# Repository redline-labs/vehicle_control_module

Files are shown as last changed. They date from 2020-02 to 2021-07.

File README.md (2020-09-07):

# Vehicle Control Module

A communication gateway and power distribution for motorsports, serving as the main electronic hub of the vehicle.

## Goals
  - Completely open-source HW and SW.  Should be a platform that anybody can hack, extend, and make their own.
  - Common parts, readily available for Digikey, Mouser, etc.  Datasheets are available without NDA.
  - Shoot for OEM level reliability and robustness, without going full ASIL alphabet soup.

## Vision
  - Controlling a circuit should be as simple as writing some logic `(engine_temp_c > 70.0f) && (vehicle_speed_mps < 5.0f)`.
  - No need for traditional fuses, relays as something like a slow-blow fuse can be done in software.
  - Plug into the vehicle using standard ethernet to debug/reconfigure/reflash.
  - Foundation for support datalogging, telemetry, and HMI.

## Hardware
Based on the Microchip [ATSAMV71Q21](https://www.microchip.com/wwwproducts/en/ATSAMV71Q21).
* (2) CAN-FD channels via [TLE9250](https://www.infineon.com/cms/en/product/transceivers/automotive-transceiver/automotive-can-transceivers/tle9250xsj/).
* (3) 100BASE-T1 channels via [TJA1100](https://www.nxp.com/products/interfaces/ethernet-/automotive-ethernet-phy-transceivers/ieee-100base-t1-compliant-automotive-ethernet-phy-transceiver:TJA1100HN).
* (1) 100BASE-TX channel via [KSZ8061MNX](https://www.microchip.com/wwwproducts/en/KSZ8061) to support debug with a laptop.
* (18) High Side drivers via [BTS50015-1TAD](https://www.infineon.com/cms/en/product/power/smart-low-side-high-side-switches/automotive-smart-high-side-switch-profet/power-profet/bts50015-1tad/).
* (2) RS-232 serial channels to connect GPS receivers and legacy IMUs.
* (8) Digital Inputs.

## Prerequisites
### MacOS
```
wget https://armkeil.blob.core.windows.net/developer/Files/downloads/gnu-rm/10-2020q2/gcc-arm-none-eabi-10-2020-q2-preview-mac.pkg

# Install.  Add `/Applications/ARM/bin/` to PATH via bash_profile.

brew install cmake
```

## Building
```
# Jump into the sw directory, create a build dir, and then jump into that.
cd sw
mkdir build
cd build

# Run CMake specifying the toolchain file.
cmake ..

# Build!
make
```

## Debugging
A configuration script under `conf/j-link` can be used with Segger Ozone to load the generated ELF on target and debug.

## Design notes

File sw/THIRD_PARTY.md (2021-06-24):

||Name||Version||License||Link||
|lua|5.4.0|MIT|https://www.lua.org/home.html|
|Advanced Software Framework|3.48|Atmel ASF License|https://www.microchip.com/mplab/avr-support/avr-and-sam-downloads-archive|
|FreeRTOS|10.4.3|MIT|https://www.freertos.org/index.html|
|FreeRTOS-Plus-TCP|2.3.3|MIT|https://www.freertos.org/index.html|

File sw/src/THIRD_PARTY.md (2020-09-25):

||Name||Version||License||Link||
|lua|5.4.0|MIT|https://www.lua.org/home.html|
|Advanced Software Framework|Atmel ASF License|https://www.microchip.com/mplab/avr-support/advanced-software-framework|
|FreeRTOS|10.4.1|MIT|https://www.freertos.org/index.html|

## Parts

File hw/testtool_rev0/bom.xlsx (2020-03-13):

Parts | Qty | Value | Package | Device | Description | MANUFACTURER_NAME | MANUFACTURER_PART_NUMBER | MOUSER_PART_NUMBER
C1, C3, C9, C92, C95 | 5 | 10uF | C0603 | GRM188R6YA106MA73J | CAPACITOR, American symbol
C101 | 1 | 0.47uF | C0603 | C1608X7R1H474K080AC | CAPACITOR, American symbol
C102 | 1 | 220nF | C0805 | C0805X223K1RECAUTO | CAPACITOR, American symbol
C16, C90, C93 | 3 | 4.7nF | C0603 | C1608C0G2A472J080AE | CAPACITOR, American symbol
C18, C87, C103, C105, C107 | 5 | 10uF | C0805 | GRM21BC8YA106ME11L | CAPACITOR, American symbol
C19, C20 | 2 | 8.2pF | C0603 | GCM1885C2A8R2DA16D | CAPACITOR, American symbol
C2, C7, C10, C11, C14, C15, C17, C66, C68, C69, C70, C75, C76, C77, C78, C91, C94, C146, C147, C156, C157, C158, C159, C160, C161, C163, C164, C166, C167, C168, C169, C170, C171, C172 | 34 | 100nF | C0603 | GCM1887U1H103JA16J | CAPACITOR, American symbol
C21, C22 | 2 | 12pF | C0603 | C0603C120K5GACTU | CAPACITOR, American symbol
C4, C5, C8, C12, C106, C162 | 6 | 1uF | C0603 | GMJ107CB7105MAHR | CAPACITOR, American symbol
C6, C13 | 2 | 47pF | C0603 | C0603C470J1GACAUTO | CAPACITOR, American symbol
C67 | 1 | 3.3uF | C0603 | C1608X5R1V335M080AC | CAPACITOR, American symbol
C71, C72, C165 | 3 | 4.7uF | C0603 | C1608JB1V475K080AC | CAPACITOR, American symbol
C73, C74 | 2 | 18nF | C0603 | GCM188R72A183KA37J | CAPACITOR, American symbol
C83, C88 | 2 | 0.47uF | C0805 | GCM21BR71H474KA55K | CAPACITOR, American symbol
C84, C85, C99, C100 | 4 | 470pF | C0805 | GCM21A5C2E471JX01D | CAPACITOR, American symbol
C86 | 1 | UCZ1K151MNQ1MS | CAPAE1360X1450N | UCZ1K151MNQ1MS | Aluminum Electrolytic Capacitors - SMD 80V 150UF 20% | Nichicon | UCZ1K151MNQ1MS | 647-UCZ1K151MNQ1MS
D1 | 1 | PESD2ETH-AXR | PESD2ETHAXR | PESD2ETH-AXR | ESD Suppressors / TVS Diodes PESD2ETH-AX/SOT4/REEL 7 Q3/T4" | Nexperia | PESD2ETH-AXR | 771-PESD2ETH-AXR
D4, D5, D6, D9 | 4 | PMEG3030EP,115 | SODFL4725X110N | PMEG3030EP,115 | Nexperia PMEG3030EP,115 SMT Schottky Diode, 30V 3A, 2-Pin SOD128 | Nexperia | PMEG3030EP,115 | 771-PMEG3030EP115
D7, D8 | 2 | SMAJ24CA-Q | DIONM5127X229N | SMAJ24CA-Q | Bourns SMAJ24CA-Q, Bi-Directional TVS Diode, 400W, 2-Pin DO-214AC | Bourns | SMAJ24CA-Q | 652-SMAJ24CA-Q
FL1 | 1 | ACT45L-201-2P-TL000 | ACT45L_1 | ACT45L-201-2P-TL000 | Common mode choke SMD 200uH 100mA 50V TDK ACT Series Shielded SMD Common Mode Line Filter 200 uH -30 %, 50 % 100mA Idc | TDK | ACT45L-201-2P-TL000 | 810-ACT45L2012PTL000
FL2, FL3, FL4 | 3 | BLM18PG330SN1D | BEADC1608X95N | BLM18PG330SN1D | BLM18_N1D Series EMI Suppression Filter 33+/-25% at 100MHz 3A @85 | Murata Electronics | BLM18PG330SN1D | 81-BLM18PG330SN1D
IC1 | 1 | SST26VF032BT-104I_SM | SOIC127P794X203-8N | SST26VF032BT-104I_SM | Microchip Technology SST26VF032BT-104I/SM 32Mbit Flash Memory Chip, 8-Pin SOIJ | Microchip | SST26VF032BT-104I/SM | 579-T26VF032BT104ISM
IC13, IC18 | 2 | TLE9250XSJXUMA1 | SOIC127P602X173-8N | TLE9250XSJXUMA1 | CAN Interface IC TRANSCEIVER | Infineon | TLE9250XSJXUMA1 | 726-TLE9250XSJXUMA1
IC2 | 1 | ATSAMV71Q21B-AABT | QFP50P2200X2200X160-144N | ATSAMV71Q21B-AABT | ARM Microcontrollers - MCU 2MB FLASH 384KB SRAM LQFP144 T/R | Microchip | ATSAMV71Q21B-AABT | 579-ATSAMV71Q21BAABT
IC3 | 1 | TJA1100HNZ | QFN50P600X600X100-37N | TJA1100HNZ | NXP - TJA1100HNZ - ETHERNET PHY, AEC-Q100, 100MBPS, HVQFN36 | Nexperia | TJA1100HNZ | 771-TJA1100HNZ
IC4 | 1 | FT2232HL | QFP50P1200X1200X160-64N | FT2232HL | Dual High Speed USB UART/FIFO IC, LQFP64 FTDI Chip FT2232HL Dual UART Interface RS232, RS422, RS485 480Mbit/s, 64-Pin, LQFP | FTDI Chip | FT2232HL
J1, J2 | 2 | 2305018-2 | TE_2305018-2 | 2305018-2 | TYPE C Right Angle Sealable SMT IPX8 3.1 GEN 2 Wire to Board USB | TE Connectivity
J3, J4, J5, J6 | 4 | TBL009-254-04GY-2GY | TBL00925404GY2GY | TBL009-254-04GY-2GY | Fixed Terminal Blocks Terminal block, screwless, 2.54, Horizontal, 4, Gray w Gray Button | CUI Devices | TBL009-254-04GY-2GY | 490-TBL00925404GY2GY
L1, L2 | 2 | 0603CS-R12XGLU | 0603CS82NXGLW | 0603CS-R12XGLU | COILCRAFT - 0603CS-R12XGLU - High Frequency Inductor, 120 nH, 0603CS Series, 300 mA, 0603 [1608 Metric], Wirewound, 0.65 ohm | COILCRAFT | 0603CS-R12XGLU | 994-0603CS-R12XGLU
L7 | 1 | XAL4020-102MEC | XAL40XX | XAL4020-102MEC | Fixed Inductors 1uH 20% 9.6A 14.60mOhms AEC-Q200 | COILCRAFT | XAL4020-102MEC | 994-XAL4020-102MEC
L8 | 1 | XAL4040-103MEC | XAL40XX | XAL4040-103MEC | Fixed Inductors XAL4040 High Current 10 uH 20 % 3.1 A | COILCRAFT | XAL4040-103MEC | 994-XAL4040-103MEC
L9 | 1 | DO3316P-103MLB | DO3316P103MLB | DO3316P-103MLB | Fixed Inductors DO3316P SMT Pwr Ind 10 uH 20 % 3.9 A | COILCRAFT | DO3316P-103MLB | 994-DO3316P-103MLB
LED1, LED4, LED5, LED6, LED7, LED11, LED12, LED13, LED14, LED15, LED16 | 11 |  | 0603 | 150060BS55040 | LED
R1, R2, R95, R96 | 4 | 60 | R0805 | ERJ-U06F60R4V | RESISTOR, American symbol
R24 | 1 | 100k | R0603 | SFR03EZPF1003 | RESISTOR, American symbol
R26, R82 | 2 | 0 | R0603 | RCS06030000Z0EC | RESISTOR, American symbol
R3, R19, R20, R21 | 4 | 49.9 | R0603 | ERJ-3EKF49R9V | RESISTOR, American symbol
R4, R22, R23 | 3 | 1k | R0603 |  | RESISTOR, American symbol
R5, R7, R10, R12, R13, R16, R18, R25, R83, R98, R103, R104, R183, R188, R193, R195, R196, R197 | 18 | 10k | R0603 |  | RESISTOR, American symbol
R6, R8, R11, R14, R15, R17 | 6 | DNP | R0603 |  | RESISTOR, American symbol
R85, R88, R89, R90, R91, R92 | 6 | 12k | R0603 | ERJ-PB3B1202V | RESISTOR, American symbol
R9, R31, R32, R86, R87 | 5 | 5.11k | R0603 | ERJ-S03F5111V | RESISTOR, American symbol
R97 | 1 | 1k | R0805 | ERJ-PB6B1001V | RESISTOR, American symbol
TC1 | 1 | TC2050-IDC | TC2050-IDC | TC2050-IDC | Tag-Connect In Circuit Programming & Debug Cable 10 Pin
U2 | 1 | LM63625 | PWP0016K_L | LM63625DQPWPRQ1 |  | Texas Instruments | LM63625DQPWPTQ1
U3 | 1 | TPS62007-Q1_DGS_10 | DGS10 | TPS62007-Q1_DGS_10 | Automotive Catalog High-Efficiency Step-Down Low Power DC-DC Converter | Texas Instruments | TPS62007-Q1_DGS_10
Y1 | 1 | NX3225SA-25MHZ-EXS00A-CS11338 | NX3225SA25MHZEXS00ACS11338 | NX3225SA-25MHZ-EXS00A-CS11338 | CRYSTAL 25MHZ 18PF SMD | NDK | NX3225SA-25MHZ-EXS00A-CS11338
Y2 | 1 | ABM8AIG-12.000MHZ-12-D2Z-T | ABM8AIG12000MHZ12D2ZT | ABM8AIG-12.000MHZ-12-D2Z-T | ABRACON - ABM8AIG-12.000MHZ-12-D2Z-T - CRYSTAL, AECQ200, 12MHZ, 12PF, 3.2X2.5MM | ABRACON | ABM8AIG-12.000MHz-12-D2Z-T | 815-ABM8AIG1212D2ZT
Y3 | 1 | ABM8AIG-12.000MHZ-1Z-T | ABM8AIG25000MHZ122ZT3 | ABM8AIG-12.000MHZ-1Z-T | Crystals 18pF 12MHz 10ppm AEC-Q200 -40C +125C | ABRACON | ABM8AIG-12.000MHZ-1Z-T | 815-M8AIG-12-1ZT

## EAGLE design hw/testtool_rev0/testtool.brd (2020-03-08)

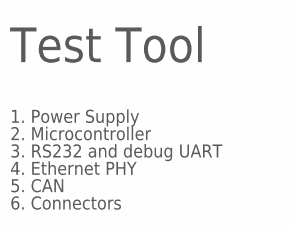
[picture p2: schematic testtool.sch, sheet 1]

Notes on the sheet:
Test Tool
1. Power Supply
2. Microcontroller
3. RS232 and debug UART
4. Ethernet PHY
5. CAN
6. Connectors

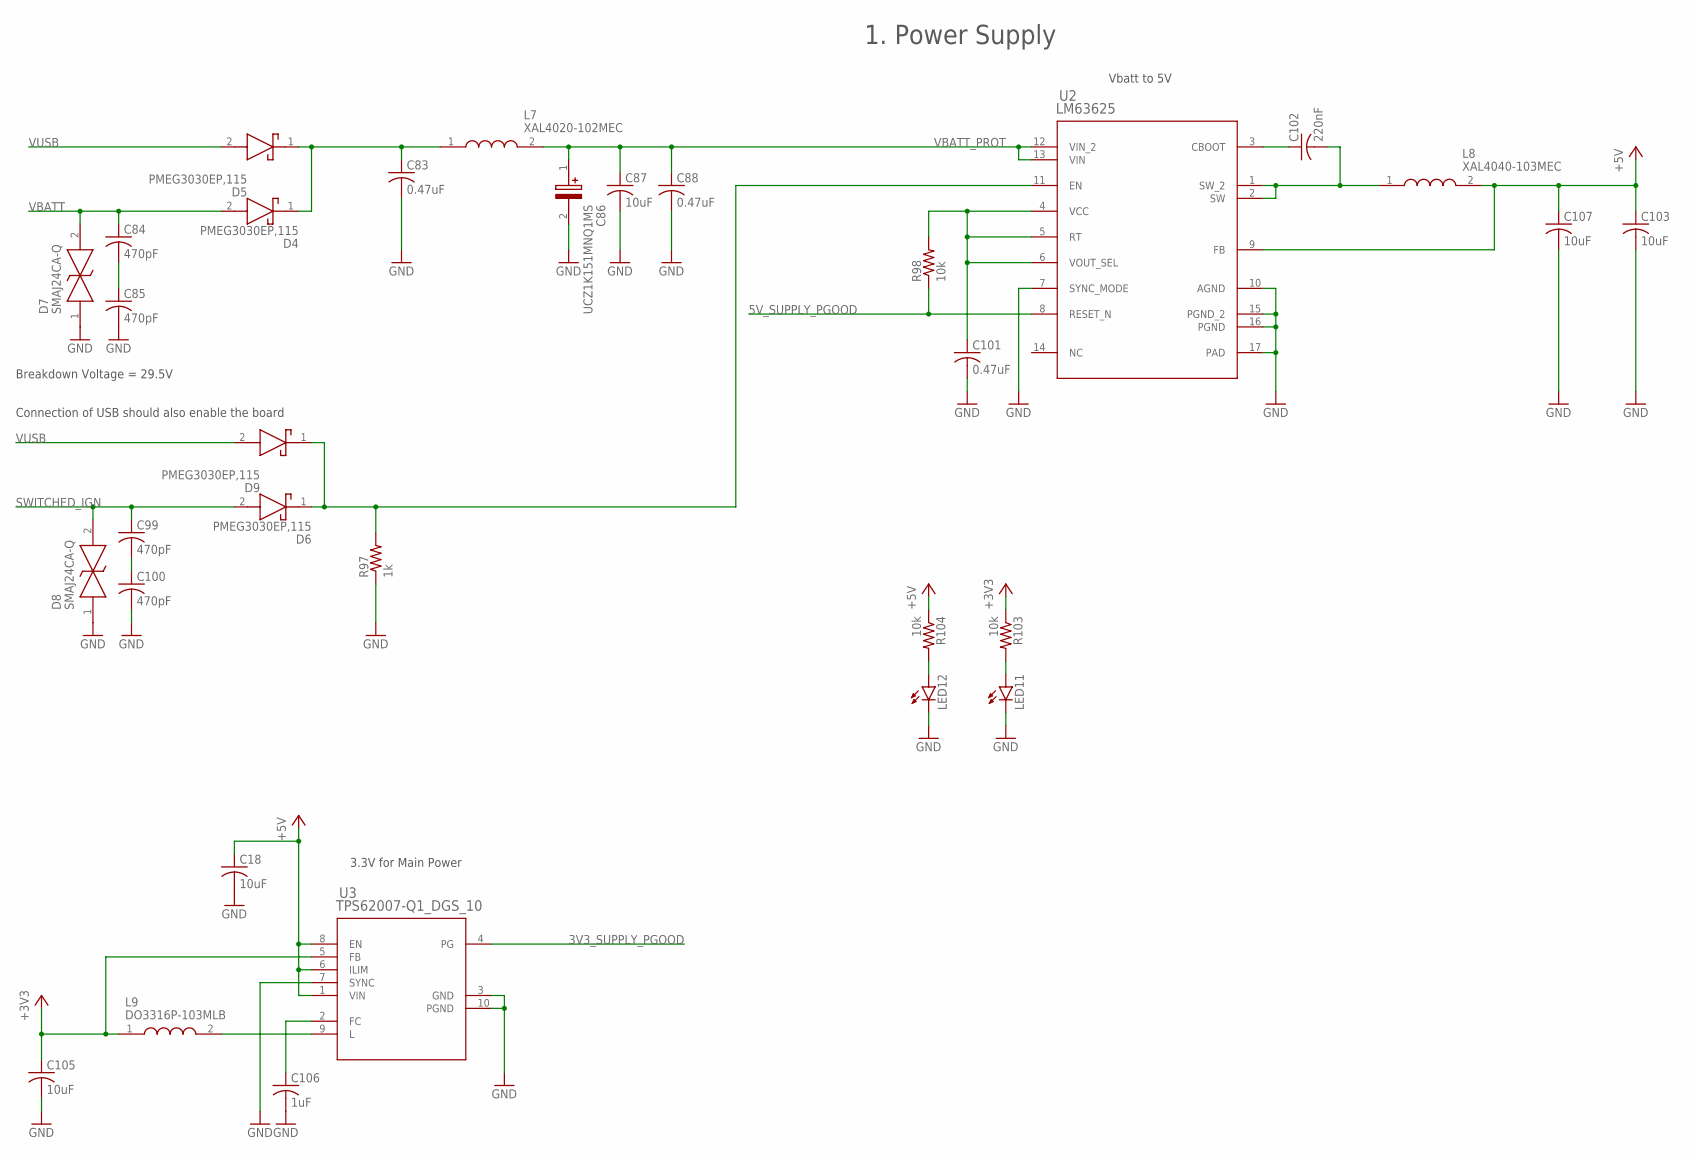
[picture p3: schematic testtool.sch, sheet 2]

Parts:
C18, C87, C103, C105, C107: 10uF; C0805
C83, C88: 0.47uF; C0805
C84, C85, C99, C100: 470pF; C0805
C86: UCZ1K151MNQ1MS; CAPAE1360X1450N
C101: 0.47uF; C0603
C102: 220nF; C0805
C106: 1uF; C0603
D4, D5, D6, D9: PMEG3030EP,115; SODFL4725X110N
D7, D8: SMAJ24CA-Q; DIONM5127X229N
L7: XAL4020-102MEC; XAL40XX
L8: XAL4040-103MEC; XAL40XX
L9: DO3316P-103MLB; DO3316P103MLB
LED11, LED12: LEDCHIPLED_0603; CHIPLED_0603
R97: 1k; R0805
R98, R103, R104: 10k; R0603
U2: LM63625; PWP0016K_L
U3: TPS62007-Q1_DGS_10; DGS10

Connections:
3V3_SUPPLY_PGOOD: U3.4 (PG); also elsewhere on the board
5V_SUPPLY_PGOOD: R98.1, U2.8 (RESET_N)
+3V3: C105.1, L9.1, R103.1, U3.5 (FB); also elsewhere on the board
+5V: C18.1, C103.1, C107.1, L8.2, R104.1, U2.9 (FB), U3.1 (VIN), U3.6 (ILIM), U3.8 (EN); also elsewhere on the board
GND: C18.2, C83.2, C85.2, C86.2 (-), C87.2, C88.2, C100.2, C101.2, C103.2, C105.2, C106.2, C107.2, D7.1, D8.1, LED11.C, LED12.C, R97.1, U2.7 (SYNC_MODE), U2.10 (AGND), U2.15 (PGND_2), U2.16 (PGND), U2.17 (PAD), U3.3 (GND), U3.7 (SYNC), U3.10 (PGND); also elsewhere on the board
unnamed: C99.2, C100.1
unnamed: D6.1 (K), D9.1 (K), R97.2, U2.11 (EN)
unnamed: C83.1, D4.1 (K), D5.1 (K), L7.1
unnamed: C84.2, C85.1
unnamed: C101.1, R98.2, U2.4 (VCC), U2.5 (RT), U2.6 (VOUT_SEL)
unnamed: L9.2, U3.9 (L)
unnamed: C102.2, L8.1, U2.1 (SW_2), U2.2 (SW)
unnamed: C106.1, U3.2 (FC)
unnamed: C102.1, U2.3 (CBOOT)
unnamed: LED11.A, R103.2
unnamed: LED12.A, R104.2
SWITCHED_IGN: C99.1, D6.2 (A), D8.2; also elsewhere on the board
VBATT: C84.1, D4.2 (A), D7.2; also elsewhere on the board
VBATT_PROT: C86.1 (+), C87.1, C88.1, L7.2, U2.12 (VIN_2), U2.13 (VIN)
VUSB: D5.2 (A), D9.2 (A); also elsewhere on the board

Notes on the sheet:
1. Power Supply
Vbatt to 5V
3.3V for Main Power
Breakdown Voltage = 29.5V
Connection of USB should also enable the board

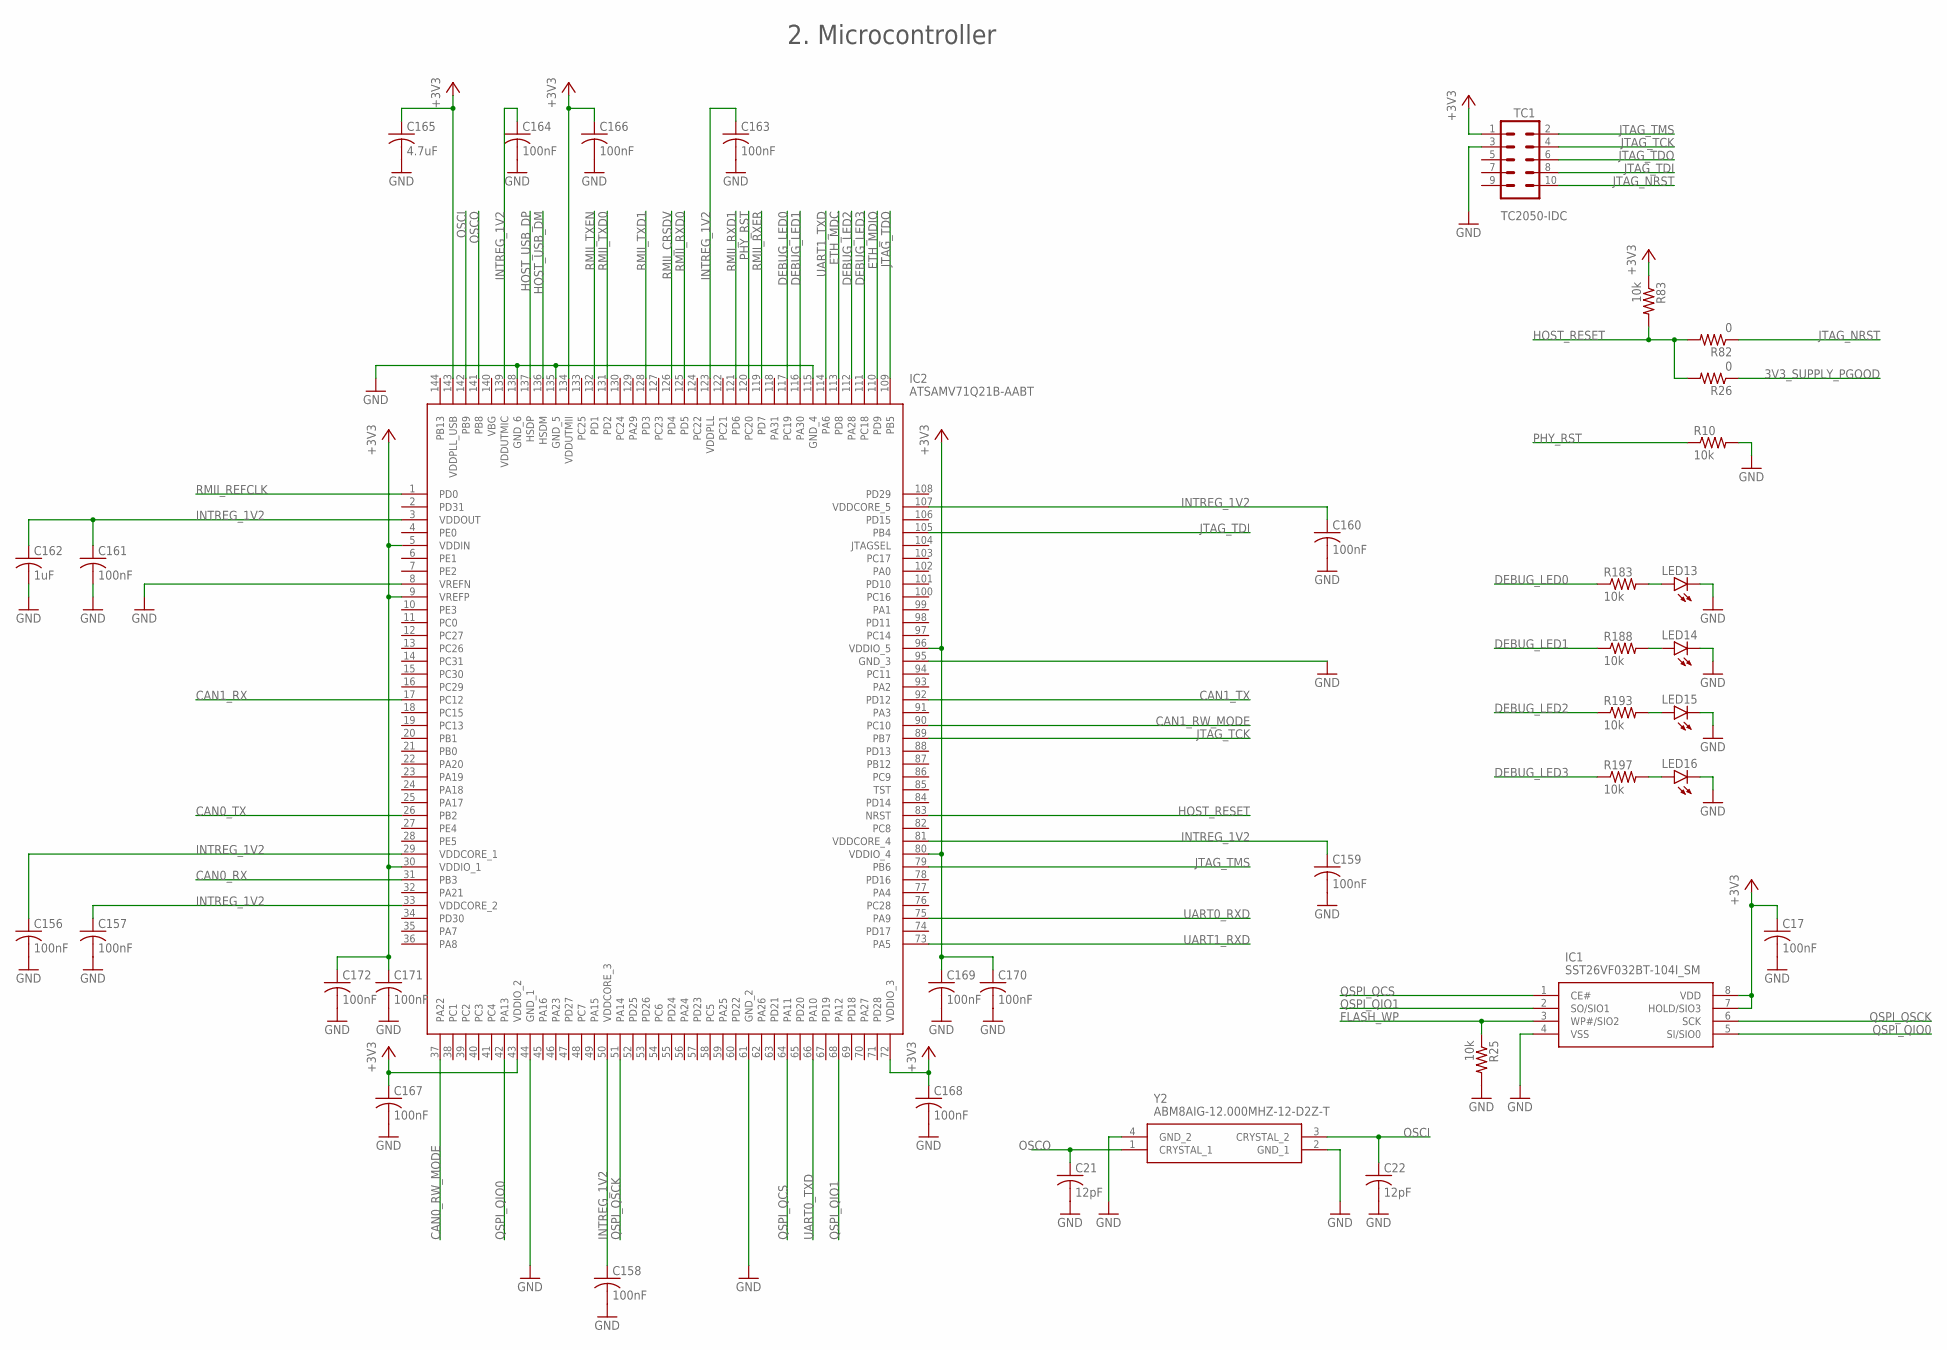
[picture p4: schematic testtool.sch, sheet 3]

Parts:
C17, C156, C157, C158, C159, C160, C161, C163, C164, C166, C167, C168, C169, C170, C171, C172: 100nF; C0603
C21, C22: 12pF; C0603
C162: 1uF; C0603
C165: 4.7uF; C0603
IC1: SST26VF032BT-104I_SM; SOIC127P794X203-8N
IC2: ATSAMV71Q21B-AABT; QFP50P2200X2200X160-144N
LED13, LED14, LED15, LED16: LEDCHIPLED_0603; CHIPLED_0603
R10, R25, R83, R183, R188, R193, R197: 10k; R0603
R26, R82: 0; R0603
TC1: TC2050-IDC
Y2: ABM8AIG-12.000MHZ-12-D2Z-T; ABM8AIG12000MHZ12D2ZT

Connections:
3V3_SUPPLY_PGOOD: R26.1; also elsewhere on the board
+3V3: C17.1, C165.1, C166.1, C167.1, C168.1, C169.1, C170.1, C171.1, C172.1, IC1.7 (HOLD/SIO3), IC1.8 (VDD), IC2.5 (VDDIN), IC2.9 (VREFP), IC2.30 (VDDIO_1), IC2.43 (VDDIO_2), IC2.72 (VDDIO_3), IC2.80 (VDDIO_4), IC2.96 (VDDIO_5), IC2.134 (VDDUTMII), IC2.143 (VDDPLL_USB), R83.1, TC1.1; also elsewhere on the board
CAN0_RW_MODE: IC2.37 (PA22); also elsewhere on the board
CAN0_RX: IC2.31 (PB3); also elsewhere on the board
CAN0_TX: IC2.26 (PB2); also elsewhere on the board
CAN1_RW_MODE: IC2.90 (PC10); also elsewhere on the board
CAN1_RX: IC2.17 (PC12); also elsewhere on the board
CAN1_TX: IC2.92 (PD12); also elsewhere on the board
DEBUG_LED0: IC2.117 (PC19), R183.1
DEBUG_LED1: IC2.116 (PA30), R188.1
DEBUG_LED2: IC2.112 (PA28), R193.1
DEBUG_LED3: IC2.111 (PC18), R197.1
ETH_MDC: IC2.113 (PD8); also elsewhere on the board
ETH_MDIO: IC2.110 (PD9); also elsewhere on the board
FLASH_WP: IC1.3 (WP#/SIO2), R25.1
GND: C17.2, C21.2, C22.2, C156.2, C157.2, C158.2, C159.2, C160.2, C161.2, C162.2, C163.2, C164.2, C165.2, C166.2, C167.2, C168.2, C169.2, C170.2, C171.2, C172.2, IC1.4 (VSS), IC2.8 (VREFN), IC2.44 (GND_1), IC2.61 (GND_2), IC2.95 (GND_3), IC2.115 (GND_4), IC2.135 (GND_5), IC2.138 (GND_6), LED13.C, LED14.C, LED15.C, LED16.C, R10.2, R25.2, TC1.3, Y2.2 (GND_1), Y2.4 (GND_2); also elsewhere on the board
HOST_RESET: IC2.83 (NRST), R26.2, R82.2, R83.2
HOST_USB_DM: IC2.136 (HSDM); also elsewhere on the board
HOST_USB_DP: IC2.137 (HSDP); also elsewhere on the board
INTREG_1V2: C156.1, C157.1, C158.1, C159.1, C160.1, C161.1, C162.1, C163.1, C164.1, IC2.3 (VDDOUT), IC2.29 (VDDCORE_1), IC2.33 (VDDCORE_2), IC2.50 (VDDCORE_3), IC2.81 (VDDCORE_4), IC2.107 (VDDCORE_5), IC2.123 (VDDPLL), IC2.139 (VDDUTMIC)
JTAG_NRST: R82.1, TC1.10
JTAG_TCK: IC2.89 (PB7), TC1.4
JTAG_TDI: IC2.105 (PB4), TC1.8
JTAG_TDO: IC2.109 (PB5), TC1.6
JTAG_TMS: IC2.79 (PB6), TC1.2
unnamed: LED13.A, R183.2
unnamed: LED14.A, R188.2
unnamed: LED15.A, R193.2
unnamed: LED16.A, R197.2
OSCI: C22.1, IC2.142 (PB9), Y2.3 (CRYSTAL_2)
OSCO: C21.1, IC2.141 (PB8), Y2.1 (CRYSTAL_1)
PHY_RST: IC2.120 (PC20), R10.1; also elsewhere on the board
QSPI_QCS: IC1.1 (CE#), IC2.64 (PA11)
QSPI_QIO0: IC1.5 (SI/SIO0), IC2.42 (PA13)
QSPI_QIO1: IC1.2 (SO/SIO1), IC2.68 (PA12)
QSPI_QSCK: IC1.6 (SCK), IC2.51 (PA14)
RMII_CRSDV: IC2.126 (PD4); also elsewhere on the board
RMII_REFCLK: IC2.1 (PD0); also elsewhere on the board
RMII_RXD0: IC2.125 (PD5); also elsewhere on the board
RMII_RXD1: IC2.121 (PD6); also elsewhere on the board
RMII_RXER: IC2.119 (PD7); also elsewhere on the board
RMII_TXD0: IC2.131 (PD2); also elsewhere on the board
RMII_TXD1: IC2.128 (PD3); also elsewhere on the board
RMII_TXEN: IC2.132 (PD1); also elsewhere on the board
UART0_RXD: IC2.75 (PA9); also elsewhere on the board
UART0_TXD: IC2.66 (PA10); also elsewhere on the board
UART1_RXD: IC2.73 (PA5); also elsewhere on the board
UART1_TXD: IC2.114 (PA6); also elsewhere on the board

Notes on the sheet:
2. Microcontroller

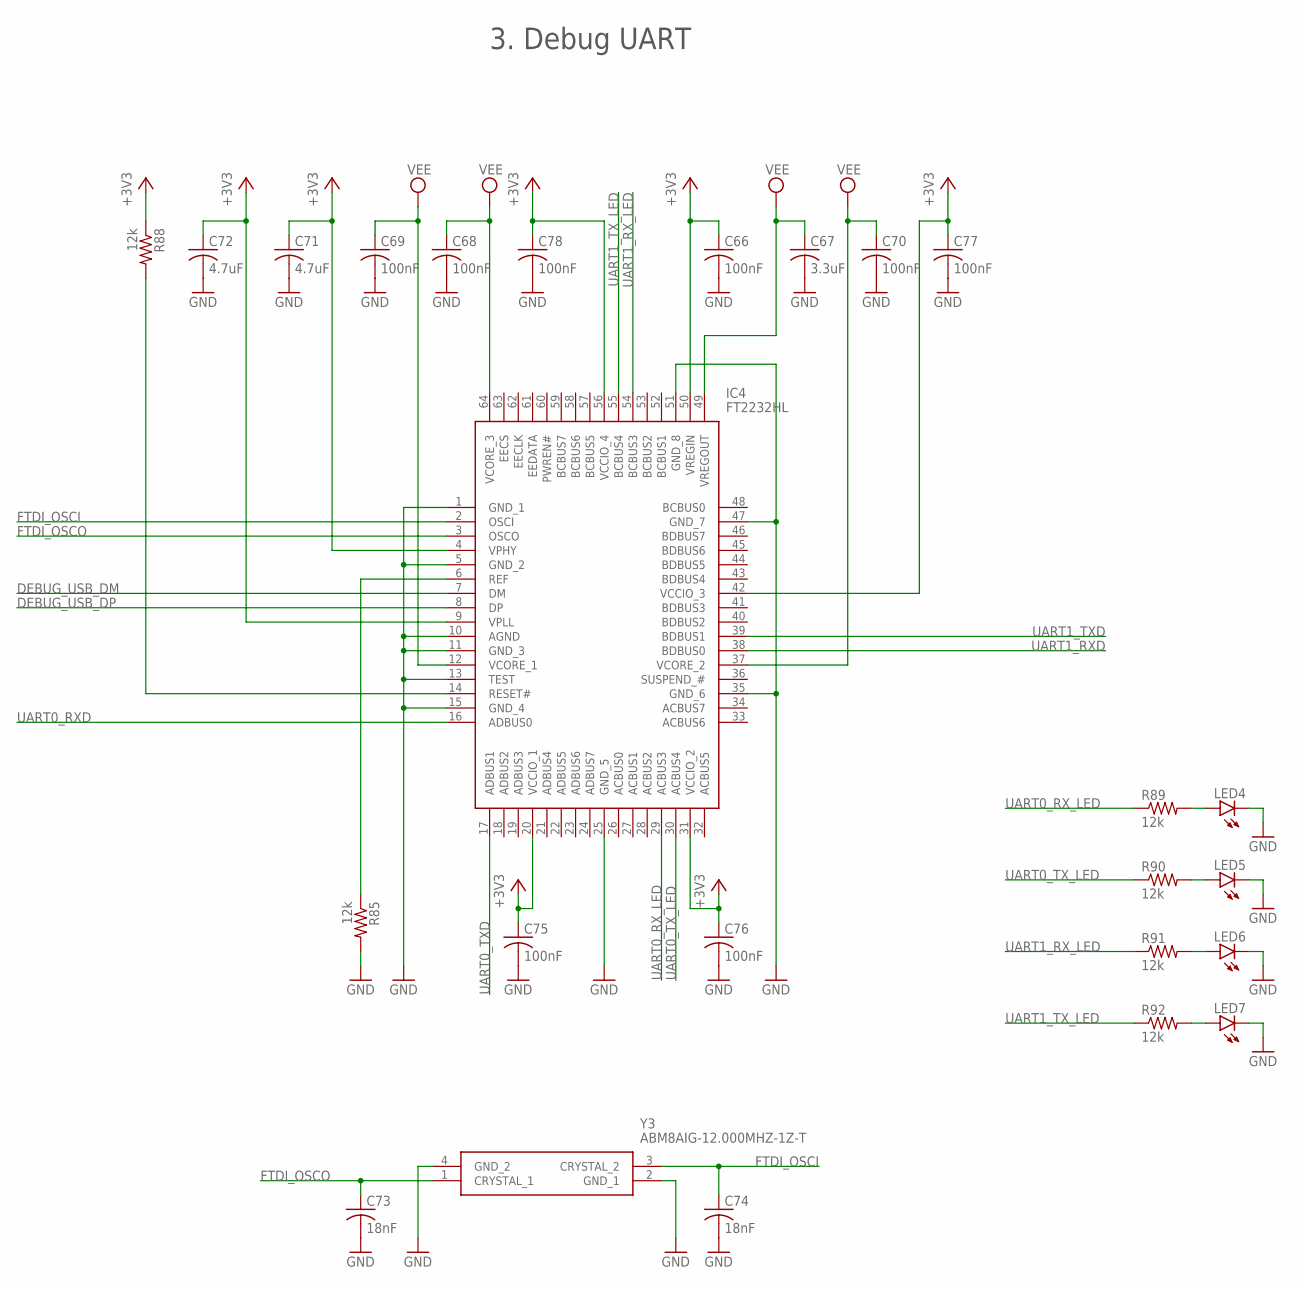
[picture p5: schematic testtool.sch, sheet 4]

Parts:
C66, C68, C69, C70, C75, C76, C77, C78: 100nF; C0603
C67: 3.3uF; C0603
C71, C72: 4.7uF; C0603
C73, C74: 18nF; C0603
IC4: FT2232HL; QFP50P1200X1200X160-64N
LED4, LED5, LED6, LED7: LEDCHIPLED_0603; CHIPLED_0603
R85, R88, R89, R90, R91, R92: 12k; R0603
Y3: ABM8AIG-12.000MHZ-1Z-T; ABM8AIG25000MHZ122ZT3

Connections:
+3V3: C66.1, C71.1, C72.1, C75.1, C76.1, C77.1, C78.1, IC4.4 (VPHY), IC4.9 (VPLL), IC4.20 (VCCIO_1), IC4.31 (VCCIO_2), IC4.42 (VCCIO_3), IC4.50 (VREGIN), IC4.56 (VCCIO_4), R88.1; also elsewhere on the board
DEBUG_USB_DM: IC4.7 (DM); also elsewhere on the board
DEBUG_USB_DP: IC4.8 (DP); also elsewhere on the board
FTDI_OSCI: C74.1, IC4.2 (OSCI), Y3.3 (CRYSTAL_2)
FTDI_OSCO: C73.1, IC4.3 (OSCO), Y3.1 (CRYSTAL_1)
GND: C66.2, C67.2, C68.2, C69.2, C70.2, C71.2, C72.2, C73.2, C74.2, C75.2, C76.2, C77.2, C78.2, IC4.1 (GND_1), IC4.5 (GND_2), IC4.10 (AGND), IC4.11 (GND_3), IC4.13 (TEST), IC4.15 (GND_4), IC4.25 (GND_5), IC4.35 (GND_6), IC4.47 (GND_7), IC4.51 (GND_8), LED4.C, LED5.C, LED6.C, LED7.C, R85.2, Y3.2 (GND_1), Y3.4 (GND_2); also elsewhere on the board
unnamed: IC4.6 (REF), R85.1
unnamed: IC4.14 (RESET#), R88.2
unnamed: LED5.A, R90.2
unnamed: LED4.A, R89.2
unnamed: LED6.A, R91.2
unnamed: LED7.A, R92.2
UART0_RXD: IC4.16 (ADBUS0); also elsewhere on the board
UART0_RX_LED: IC4.29 (ACBUS3), R89.1
UART0_TXD: IC4.17 (ADBUS1); also elsewhere on the board
UART0_TX_LED: IC4.30 (ACBUS4), R90.1
UART1_RXD: IC4.38 (BDBUS0); also elsewhere on the board
UART1_RX_LED: IC4.54 (BCBUS3), R91.1
UART1_TXD: IC4.39 (BDBUS1); also elsewhere on the board
UART1_TX_LED: IC4.55 (BCBUS4), R92.1
VEE: C67.1, C68.1, C69.1, C70.1, IC4.12 (VCORE_1), IC4.37 (VCORE_2), IC4.49 (VREGOUT), IC4.64 (VCORE_3)

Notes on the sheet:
3. Debug UART

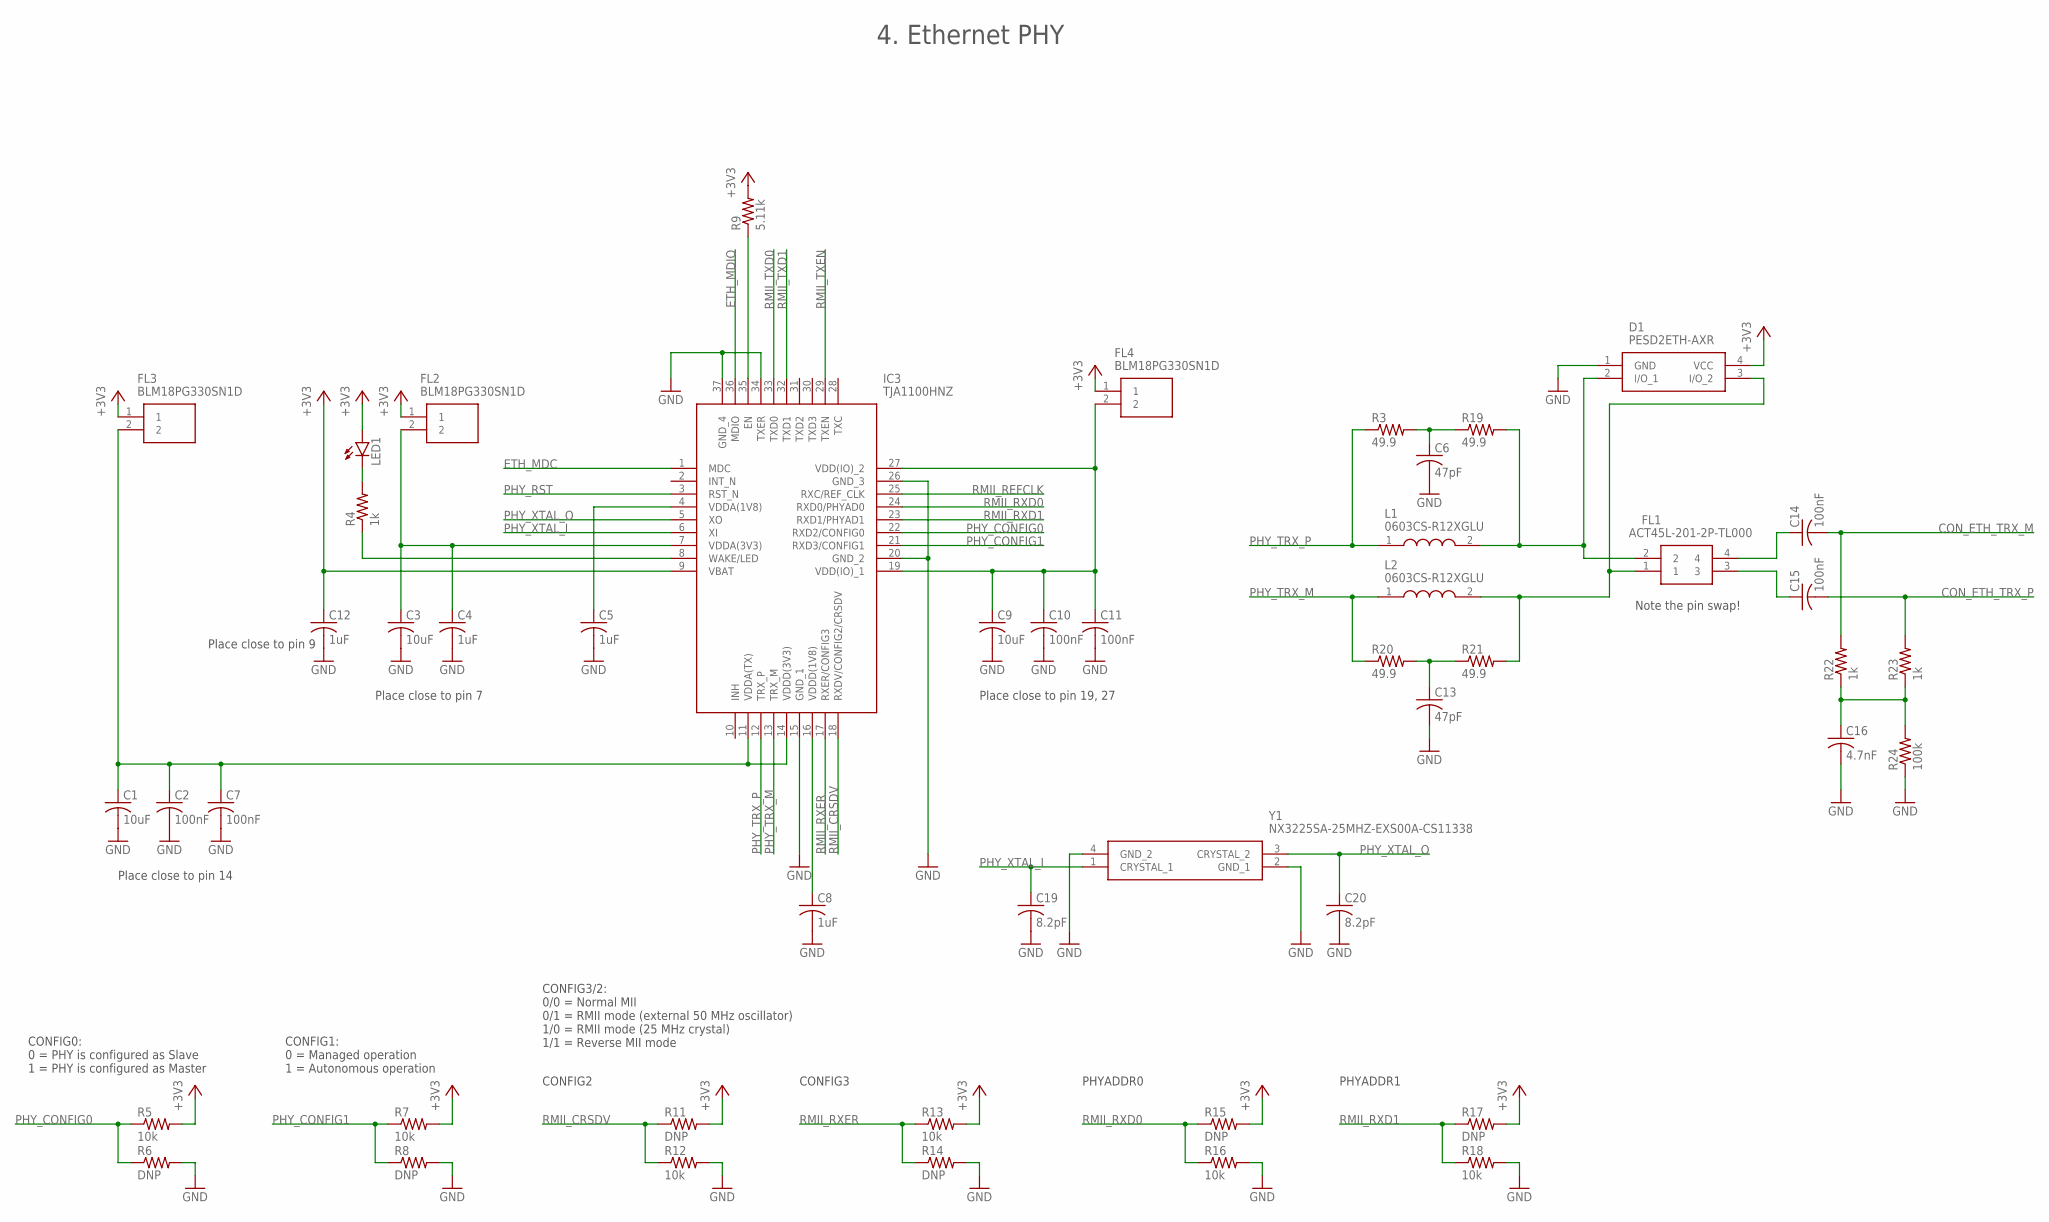
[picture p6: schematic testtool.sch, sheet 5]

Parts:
C1, C3, C9: 10uF; C0603
C2, C7, C10, C11, C14, C15: 100nF; C0603
C4, C5, C8, C12: 1uF; C0603
C6, C13: 47pF; C0603
C16: 4.7nF; C0603
C19, C20: 8.2pF; C0603
D1: PESD2ETH-AXR; PESD2ETHAXR
FL1: ACT45L-201-2P-TL000; ACT45L_1
FL2, FL3, FL4: BLM18PG330SN1D; BEADC1608X95N
IC3: TJA1100HNZ; QFN50P600X600X100-37N
L1, L2: 0603CS-R12XGLU; 0603CS82NXGLW
LED1: LEDCHIPLED_0603; CHIPLED_0603
R3, R19, R20, R21: 49.9; R0603
R4, R22, R23: 1k; R0603
R5, R7, R12, R13, R16, R18: 10k; R0603
R6, R8, R11, R14, R15, R17: DNP; R0603
R9: 5.11k; R0603
R24: 100k; R0603
Y1: NX3225SA-25MHZ-EXS00A-CS11338; NX3225SA25MHZEXS00ACS11338

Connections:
+3V3: C12.1, D1.4 (VCC), FL2.1, FL3.1, FL4.1, IC3.9 (VBAT), LED1.A, R5.2, R7.2, R9.2, R11.2, R13.2, R15.2, R17.2; also elsewhere on the board
CON_ETH_TRX_M: C14.2, R22.2; also elsewhere on the board
CON_ETH_TRX_P: C15.2, R23.2; also elsewhere on the board
ETH_MDC: IC3.1 (MDC); also elsewhere on the board
ETH_MDIO: IC3.36 (MDIO); also elsewhere on the board
GND: C1.2, C2.2, C3.2, C4.2, C5.2, C6.2, C7.2, C8.2, C9.2, C10.2, C11.2, C12.2, C13.2, C16.2, C19.2, C20.2, D1.1 (GND), IC3.15 (GND_1), IC3.20 (GND_2), IC3.26 (GND_3), IC3.34 (TXER), IC3.37 (GND_4), R6.2, R8.2, R12.2, R14.2, R16.2, R18.2, R24.1, Y1.2 (GND_1), Y1.4 (GND_2); also elsewhere on the board
unnamed: LED1.C, R4.2
unnamed: C5.1, IC3.4 (VDDA(1V8))
unnamed: IC3.8 (WAKE/LED), R4.1
unnamed: C8.1, IC3.16 (VDDD(1V8))
unnamed: C3.1, C4.1, FL2.2, IC3.7 (VDDA(3V3))
unnamed: C1.1, C2.1, C7.1, FL3.2, IC3.11 (VDDA(TX)), IC3.14 (VDDD(3V3))
unnamed: C9.1, C10.1, C11.1, FL4.2, IC3.19 (VDD(IO)_1), IC3.27 (VDD(IO)_2)
unnamed: IC3.35 (EN), R9.1
unnamed: D1.3 (I/O_2), FL1.1, L2.2, R21.2
unnamed: D1.2 (I/O_1), FL1.2, L1.2, R19.2
unnamed: C6.1, R3.2, R19.1
unnamed: C13.1, R20.2, R21.1
unnamed: C14.1, FL1.4
unnamed: C15.1, FL1.3
unnamed: C16.1, R22.1, R23.1, R24.2
PHY_CONFIG0: IC3.22 (RXD2/CONFIG0), R5.1, R6.1
PHY_CONFIG1: IC3.21 (RXD3/CONFIG1), R7.1, R8.1
PHY_RST: IC3.3 (RST_N); also elsewhere on the board
PHY_TRX_M: IC3.13 (TRX_M), L2.1, R20.1
PHY_TRX_P: IC3.12 (TRX_P), L1.1, R3.1
PHY_XTAL_I: C19.1, IC3.6 (XI), Y1.1 (CRYSTAL_1)
PHY_XTAL_O: C20.1, IC3.5 (XO), Y1.3 (CRYSTAL_2)
RMII_CRSDV: IC3.18 (RXDV/CONFIG2/CRSDV), R11.1, R12.1; also elsewhere on the board
RMII_REFCLK: IC3.25 (RXC/REF_CLK); also elsewhere on the board
RMII_RXD0: IC3.24 (RXD0/PHYAD0), R15.1, R16.1; also elsewhere on the board
RMII_RXD1: IC3.23 (RXD1/PHYAD1), R17.1, R18.1; also elsewhere on the board
RMII_RXER: IC3.17 (RXER/CONFIG3), R13.1, R14.1; also elsewhere on the board
RMII_TXD0: IC3.33 (TXD0); also elsewhere on the board
RMII_TXD1: IC3.32 (TXD1); also elsewhere on the board
RMII_TXEN: IC3.29 (TXEN); also elsewhere on the board

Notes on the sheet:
Place close to pin 7
Place close to pin 9
Place close to pin 14
Place close to pin 19, 27
CONFIG0: 0 = PHY is configured as Slave 1 = PHY is configured as Master
CONFIG1: 0 = Managed operation 1 = Autonomous operation
Note the pin swap!
4. Ethernet PHY
CONFIG3/2: 0/0 = Normal MII 0/1 = RMII mode (external 50 MHz oscillator) 1/0 = RMII mode (25 MHz crystal) 1/1 = Reverse MII mode
CONFIG2
CONFIG3
PHYADDR0
PHYADDR1

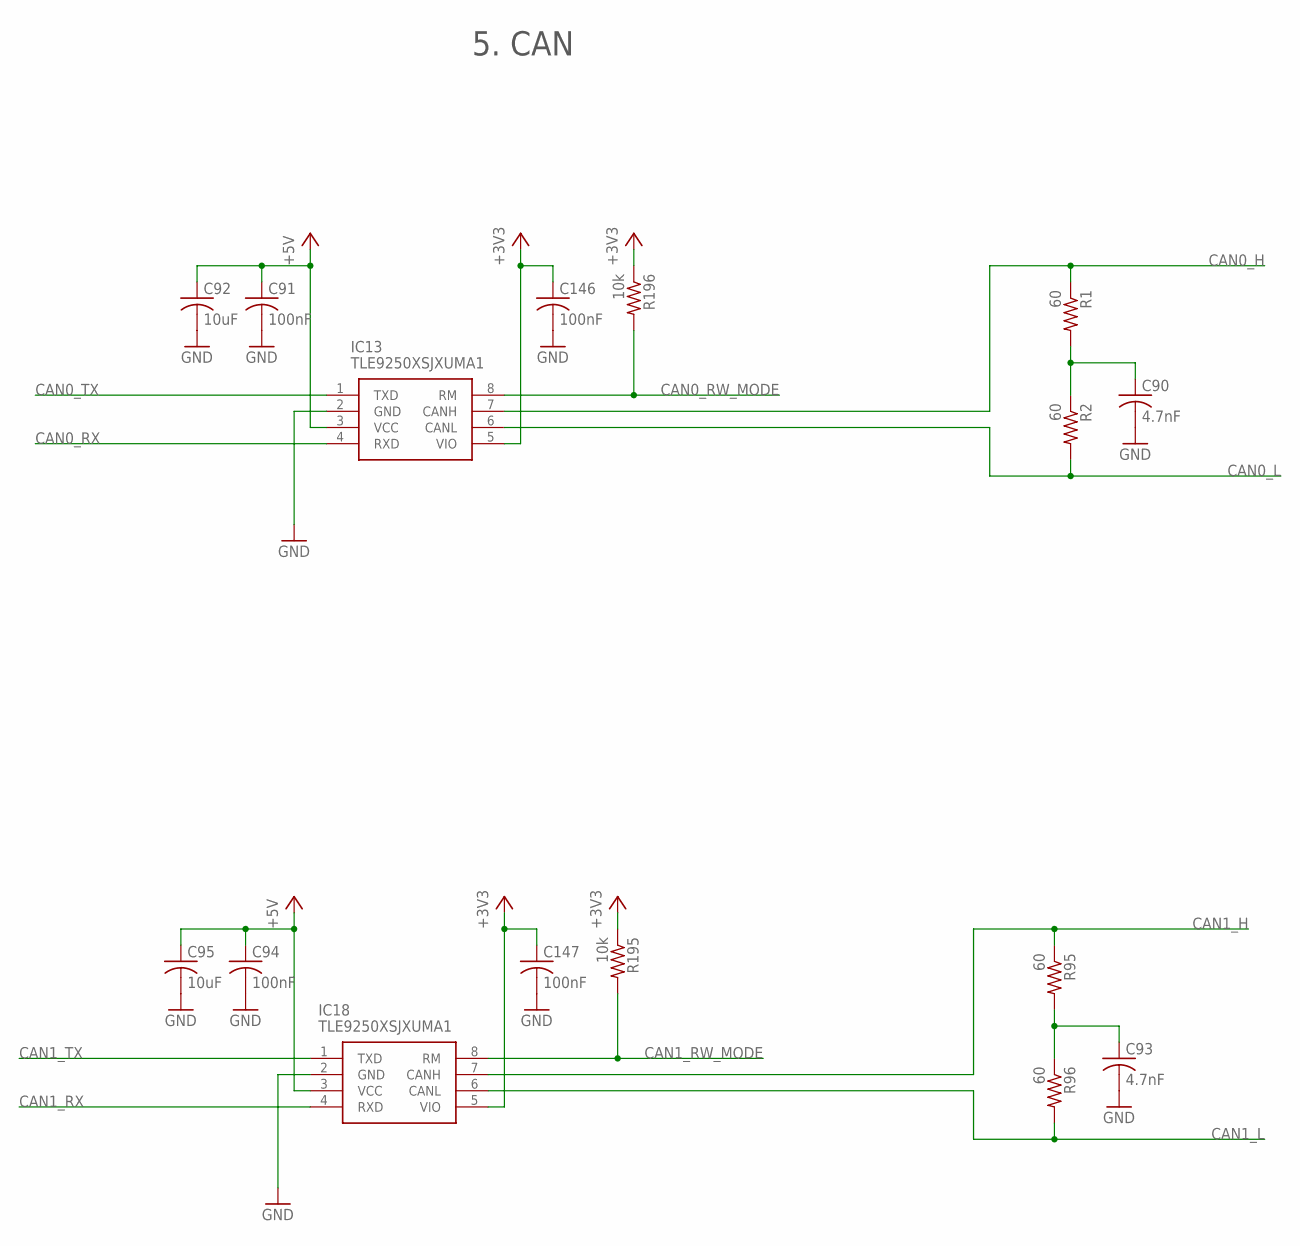
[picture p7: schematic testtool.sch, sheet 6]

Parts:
C90, C93: 4.7nF; C0603
C91, C94, C146, C147: 100nF; C0603
C92, C95: 10uF; C0603
IC13, IC18: TLE9250XSJXUMA1; SOIC127P602X173-8N
R1, R2, R95, R96: 60; R0805
R195, R196: 10k; R0603

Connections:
+3V3: C146.1, C147.1, IC13.5 (VIO), IC18.5 (VIO), R195.1, R196.1; also elsewhere on the board
+5V: C91.1, C92.1, C94.1, C95.1, IC13.3 (VCC), IC18.3 (VCC); also elsewhere on the board
CAN0_H: IC13.7 (CANH), R1.1; also elsewhere on the board
CAN0_L: IC13.6 (CANL), R2.2; also elsewhere on the board
CAN0_RW_MODE: IC13.8 (RM), R196.2; also elsewhere on the board
CAN0_RX: IC13.4 (RXD); also elsewhere on the board
CAN0_TX: IC13.1 (TXD); also elsewhere on the board
CAN1_H: IC18.7 (CANH), R95.1; also elsewhere on the board
CAN1_L: IC18.6 (CANL), R96.2; also elsewhere on the board
CAN1_RW_MODE: IC18.8 (RM), R195.2; also elsewhere on the board
CAN1_RX: IC18.4 (RXD); also elsewhere on the board
CAN1_TX: IC18.1 (TXD); also elsewhere on the board
GND: C90.2, C91.2, C92.2, C93.2, C94.2, C95.2, C146.2, C147.2, IC13.2 (GND), IC18.2 (GND); also elsewhere on the board
unnamed: C93.1, R95.2, R96.1
unnamed: C90.1, R1.2, R2.1

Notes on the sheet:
5. CAN

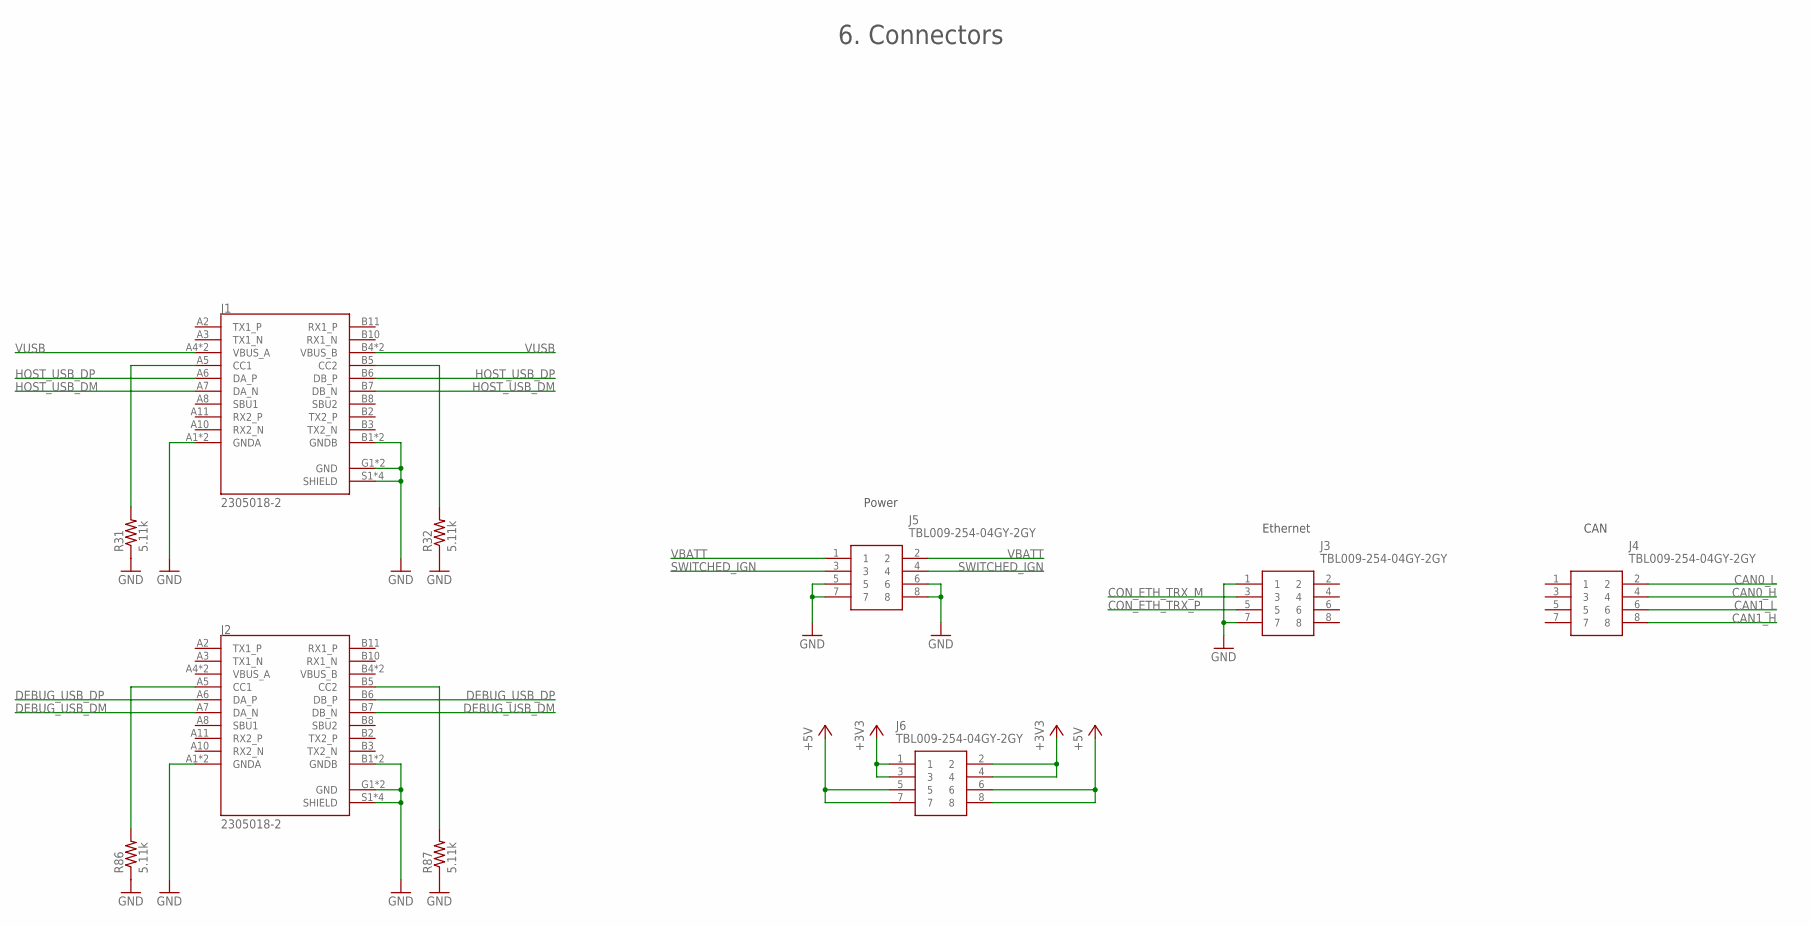
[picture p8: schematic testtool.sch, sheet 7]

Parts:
J1, J2: 2305018-2; TE_2305018-2
J3, J4, J5, J6: TBL009-254-04GY-2GY; TBL00925404GY2GY
R31, R32, R86, R87: 5.11k; R0603

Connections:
+3V3: J6.1, J6.2, J6.3, J6.4; also elsewhere on the board
+5V: J6.5, J6.6, J6.7, J6.8; also elsewhere on the board
CAN0_H: J4.4; also elsewhere on the board
CAN0_L: J4.2; also elsewhere on the board
CAN1_H: J4.8; also elsewhere on the board
CAN1_L: J4.6; also elsewhere on the board
CON_ETH_TRX_M: J3.3; also elsewhere on the board
CON_ETH_TRX_P: J3.5; also elsewhere on the board
DEBUG_USB_DM: J2.A7 (DA_N), J2.B7 (DB_N); also elsewhere on the board
DEBUG_USB_DP: J2.A6 (DA_P), J2.B6 (DB_P); also elsewhere on the board
GND: J1.A1 (GNDA), J1.A12 (GNDA), J1.B1 (GNDB), J1.B12 (GNDB), J1.G1 (GND), J1.G2 (GND), J1.S1 (SHIELD), J1.S2 (SHIELD), J1.S3 (SHIELD), J1.S4 (SHIELD), J2.A1 (GNDA), J2.A12 (GNDA), J2.B1 (GNDB), J2.B12 (GNDB), J2.G1 (GND), J2.G2 (GND), J2.S1 (SHIELD), J2.S2 (SHIELD), J2.S3 (SHIELD), J2.S4 (SHIELD), J3.1, J3.7, J5.5, J5.6, J5.7, J5.8, R31.1, R32.1, R86.1, R87.1; also elsewhere on the board
HOST_USB_DM: J1.A7 (DA_N), J1.B7 (DB_N); also elsewhere on the board
HOST_USB_DP: J1.A6 (DA_P), J1.B6 (DB_P); also elsewhere on the board
unnamed: J1.A5 (CC1), R31.2
unnamed: J1.B5 (CC2), R32.2
unnamed: J2.A5 (CC1), R86.2
unnamed: J2.B5 (CC2), R87.2
SWITCHED_IGN: J5.3, J5.4; also elsewhere on the board
VBATT: J5.1, J5.2; also elsewhere on the board
VUSB: J1.A4 (VBUS_A), J1.A9 (VBUS_A), J1.B4 (VBUS_B), J1.B9 (VBUS_B); also elsewhere on the board

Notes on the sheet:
Power
Ethernet
CAN
6. Connectors

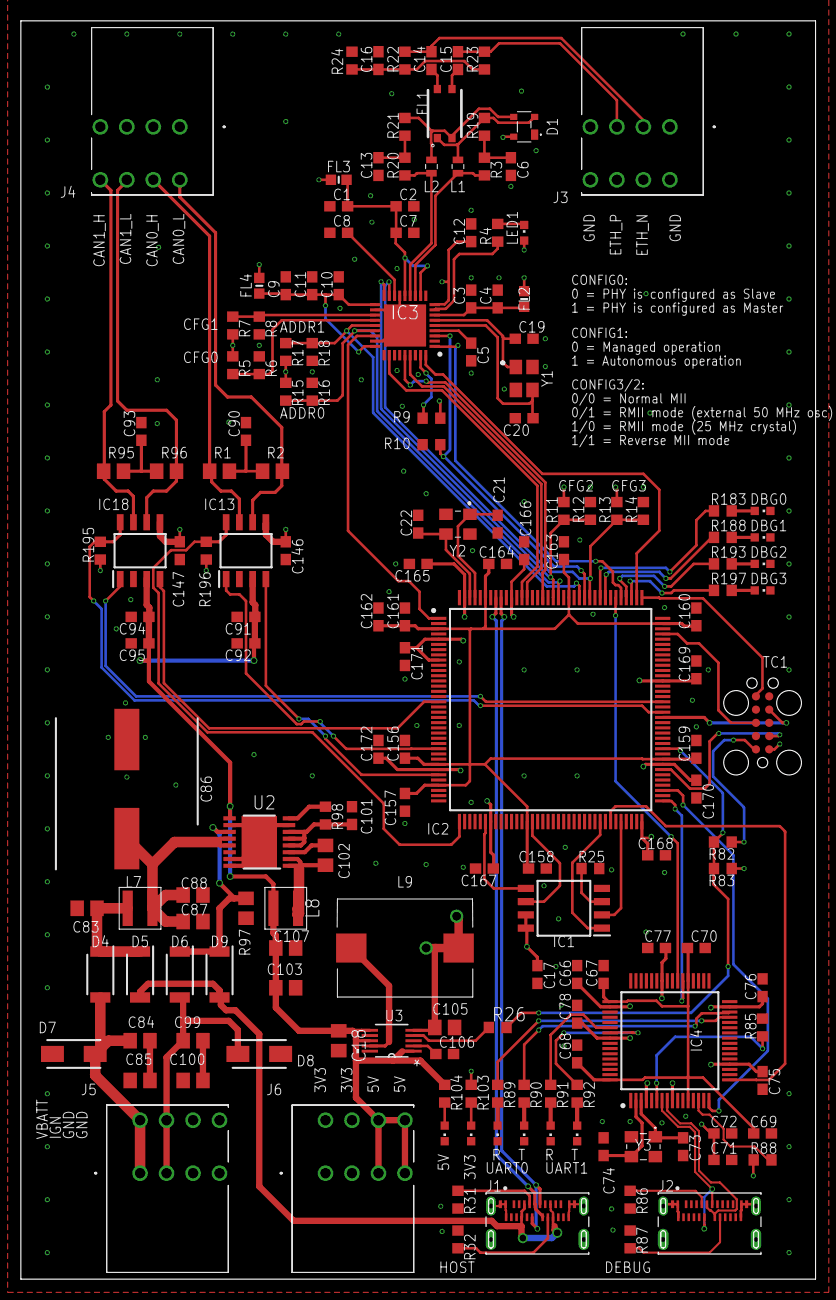
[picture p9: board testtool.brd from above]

Board: 4 copper layers, 76.2 x 120.6 mm, 169 parts (0 on the bottom side), 113 nets.

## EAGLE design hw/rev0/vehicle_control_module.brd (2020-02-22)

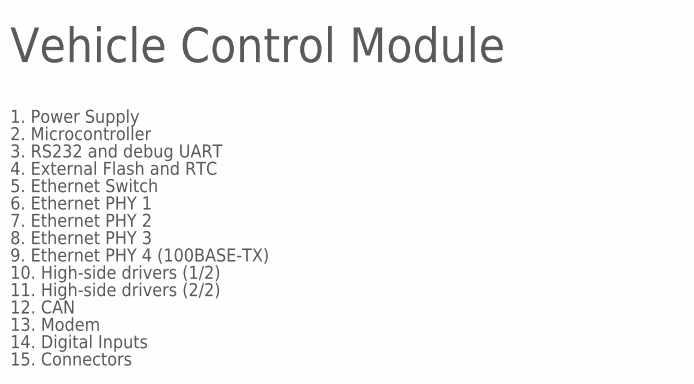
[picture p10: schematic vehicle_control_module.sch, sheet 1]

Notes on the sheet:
Vehicle Control Module
1. Power Supply
2. Microcontroller
3. RS232 and debug UART
4. External Flash and RTC
5. Ethernet Switch
6. Ethernet PHY 1
7. Ethernet PHY 2
8. Ethernet PHY 3
9. Ethernet PHY 4 (100BASE-TX)
10. High-side drivers (1/2)
12. CAN
13. Modem
15. Connectors
11. High-side drivers (2/2)
14. Digital Inputs

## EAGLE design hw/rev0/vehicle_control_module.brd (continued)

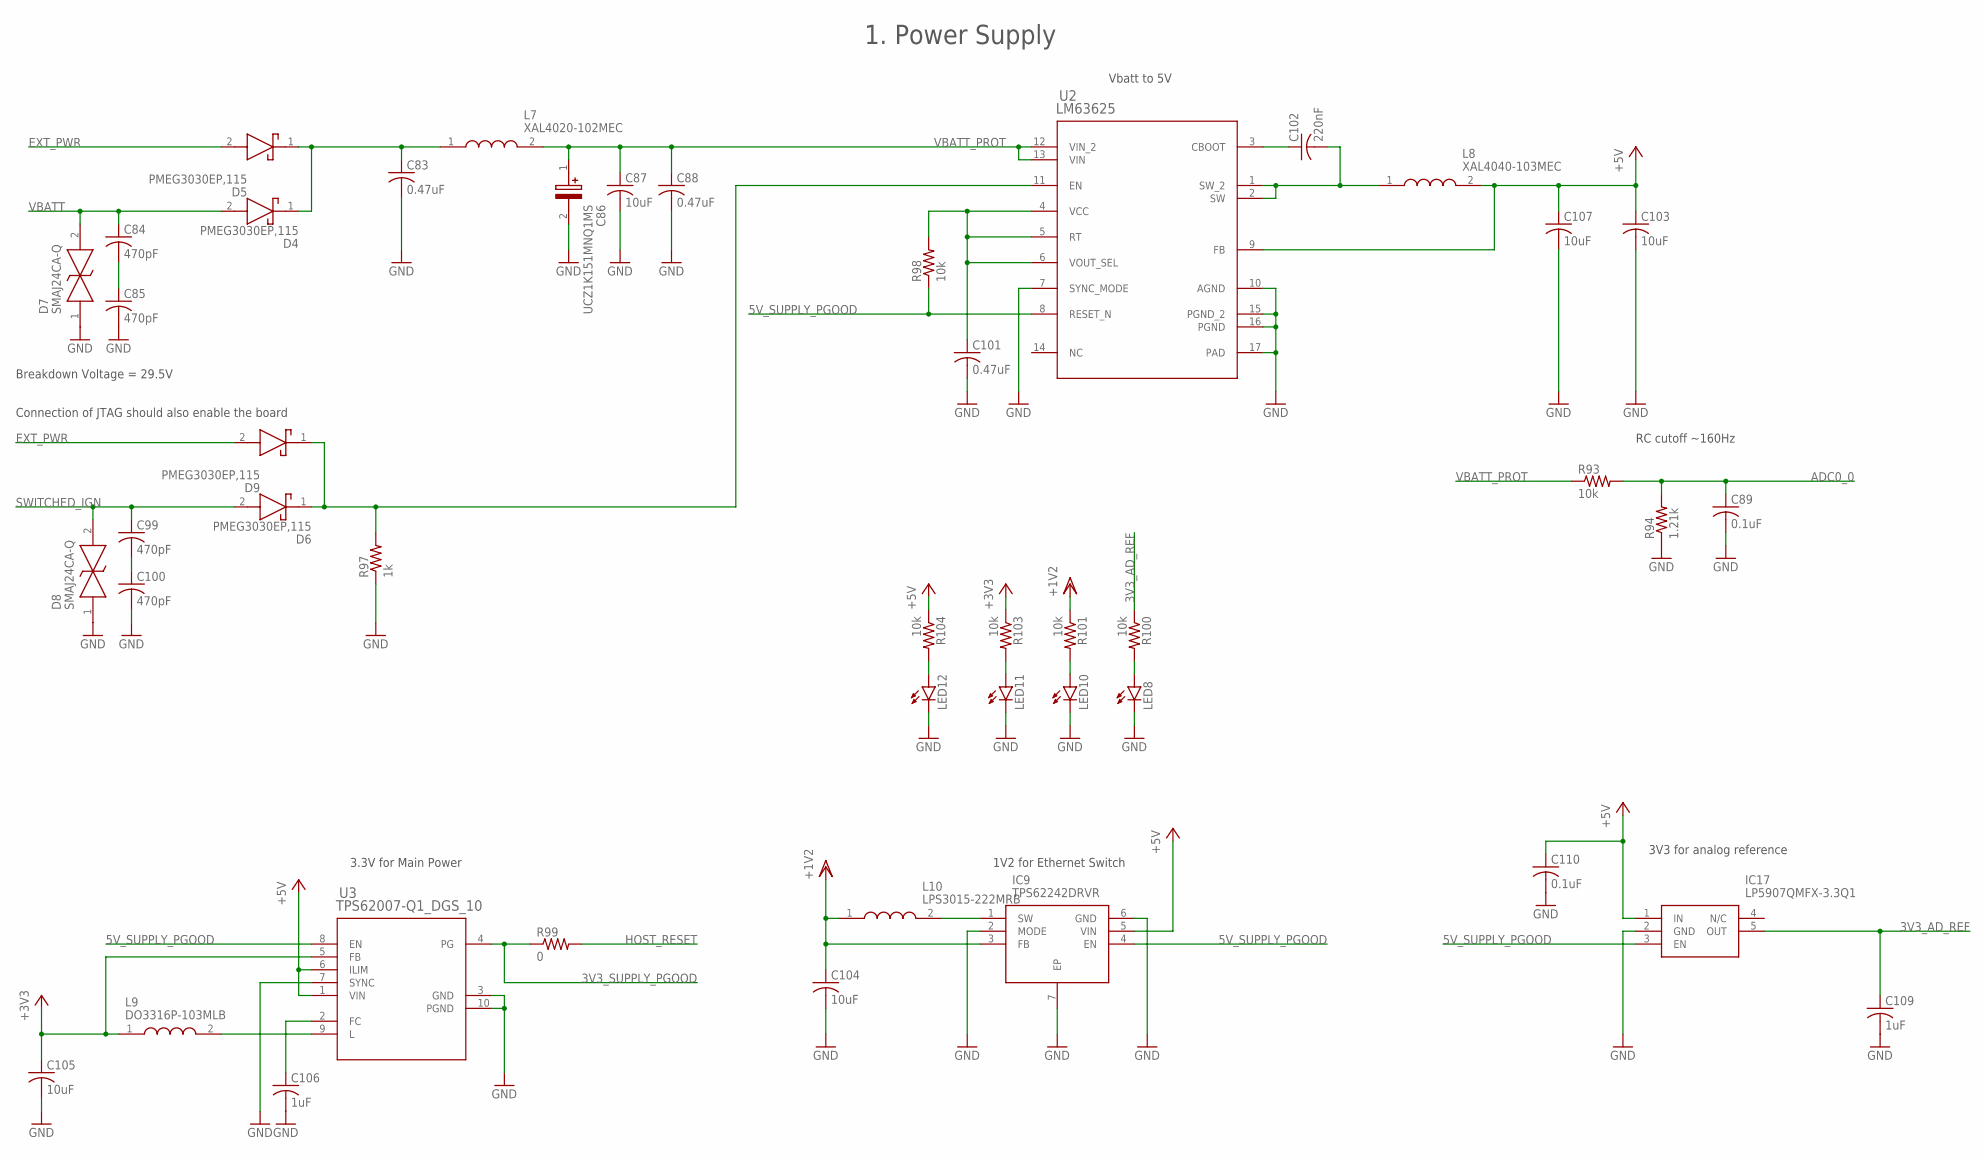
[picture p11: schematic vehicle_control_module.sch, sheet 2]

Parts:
C83, C88: 0.47uF; C0805
C84, C85, C99, C100: 470pF; C0805
C86: UCZ1K151MNQ1MS; CAPAE1360X1450N
C87, C103, C104, C105, C107: 10uF; C0805
C89, C110: 0.1uF; C0603
C101: 0.47uF; C0603
C102: 220nF; C0805
C106, C109: 1uF; C0603
D4, D5, D6, D9: PMEG3030EP,115; SODFL4725X110N
D7, D8: SMAJ24CA-Q; DIONM5127X229N
IC9: TPS62242DRVR; SON65P200X200X80-7N
IC17: LP5907QMFX-3.3Q1; SOT95P280X145-5N
L7: XAL4020-102MEC; XAL40XX
L8: XAL4040-103MEC; XAL40XX
L9: DO3316P-103MLB; DO3316P103MLB
L10: LPS3015-222MRB; LPS3015
LED8, LED10, LED11, LED12: LEDCHIPLED_0603; CHIPLED_0603
R93, R98, R100, R101, R103, R104: 10k; R0603
R94: 1.21k; R0603
R97: 1k; R0805
R99: 0; R0603
U2: LM63625; PWP0016K_L
U3: TPS62007-Q1_DGS_10; DGS10

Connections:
3V3_AD_REF: C109.1, IC17.5 (OUT), R100.1; also elsewhere on the board
3V3_SUPPLY_PGOOD: R99.1, U3.4 (PG)
5V_SUPPLY_PGOOD: IC9.4 (EN), IC17.3 (EN), R98.1, U2.8 (RESET_N), U3.8 (EN)
+3V3: C105.1, L9.1, R103.1, U3.5 (FB); also elsewhere on the board
+5V: C103.1, C107.1, C110.1, IC9.5 (VIN), IC17.1 (IN), L8.2, R104.1, U2.9 (FB), U3.1 (VIN), U3.6 (ILIM); also elsewhere on the board
ADC0_0: C89.1, R93.2, R94.2; also elsewhere on the board
EXT_PWR: D5.2 (A), D9.2 (A); also elsewhere on the board
GND: C83.2, C85.2, C86.2 (-), C87.2, C88.2, C89.2, C100.2, C101.2, C103.2, C104.2, C105.2, C106.2, C107.2, C109.2, C110.2, D7.1, D8.1, IC9.2 (MODE), IC9.6 (GND), IC9.7 (EP), IC17.2 (GND), LED8.C, LED10.C, LED11.C, LED12.C, R94.1, R97.1, U2.7 (SYNC_MODE), U2.10 (AGND), U2.15 (PGND_2), U2.16 (PGND), U2.17 (PAD), U3.3 (GND), U3.7 (SYNC), U3.10 (PGND); also elsewhere on the board
HOST_RESET: R99.2; also elsewhere on the board
unnamed: C99.2, C100.1
unnamed: D6.1 (K), D9.1 (K), R97.2, U2.11 (EN)
unnamed: C83.1, D4.1 (K), D5.1 (K), L7.1
unnamed: C84.2, C85.1
unnamed: C101.1, R98.2, U2.4 (VCC), U2.5 (RT), U2.6 (VOUT_SEL)
unnamed: L9.2, U3.9 (L)
unnamed: C102.2, L8.1, U2.1 (SW_2), U2.2 (SW)
unnamed: C106.1, U3.2 (FC)
unnamed: C102.1, U2.3 (CBOOT)
unnamed: LED8.A, R100.2
unnamed: IC9.1 (SW), L10.2
unnamed: LED10.A, R101.2
unnamed: LED11.A, R103.2
unnamed: LED12.A, R104.2
SWITCHED_IGN: C99.1, D6.2 (A), D8.2
VBATT: C84.1, D4.2 (A), D7.2; also elsewhere on the board
VBATT_PROT: C86.1 (+), C87.1, C88.1, L7.2, R93.1, U2.12 (VIN_2), U2.13 (VIN)
VDD: C104.1, IC9.3 (FB), L10.1, R101.1; also elsewhere on the board

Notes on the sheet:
1. Power Supply
1V2 for Ethernet Switch
Vbatt to 5V
3.3V for Main Power
3V3 for analog reference
Breakdown Voltage = 29.5V
RC cutoff ~160Hz
Connection of JTAG should also enable the board

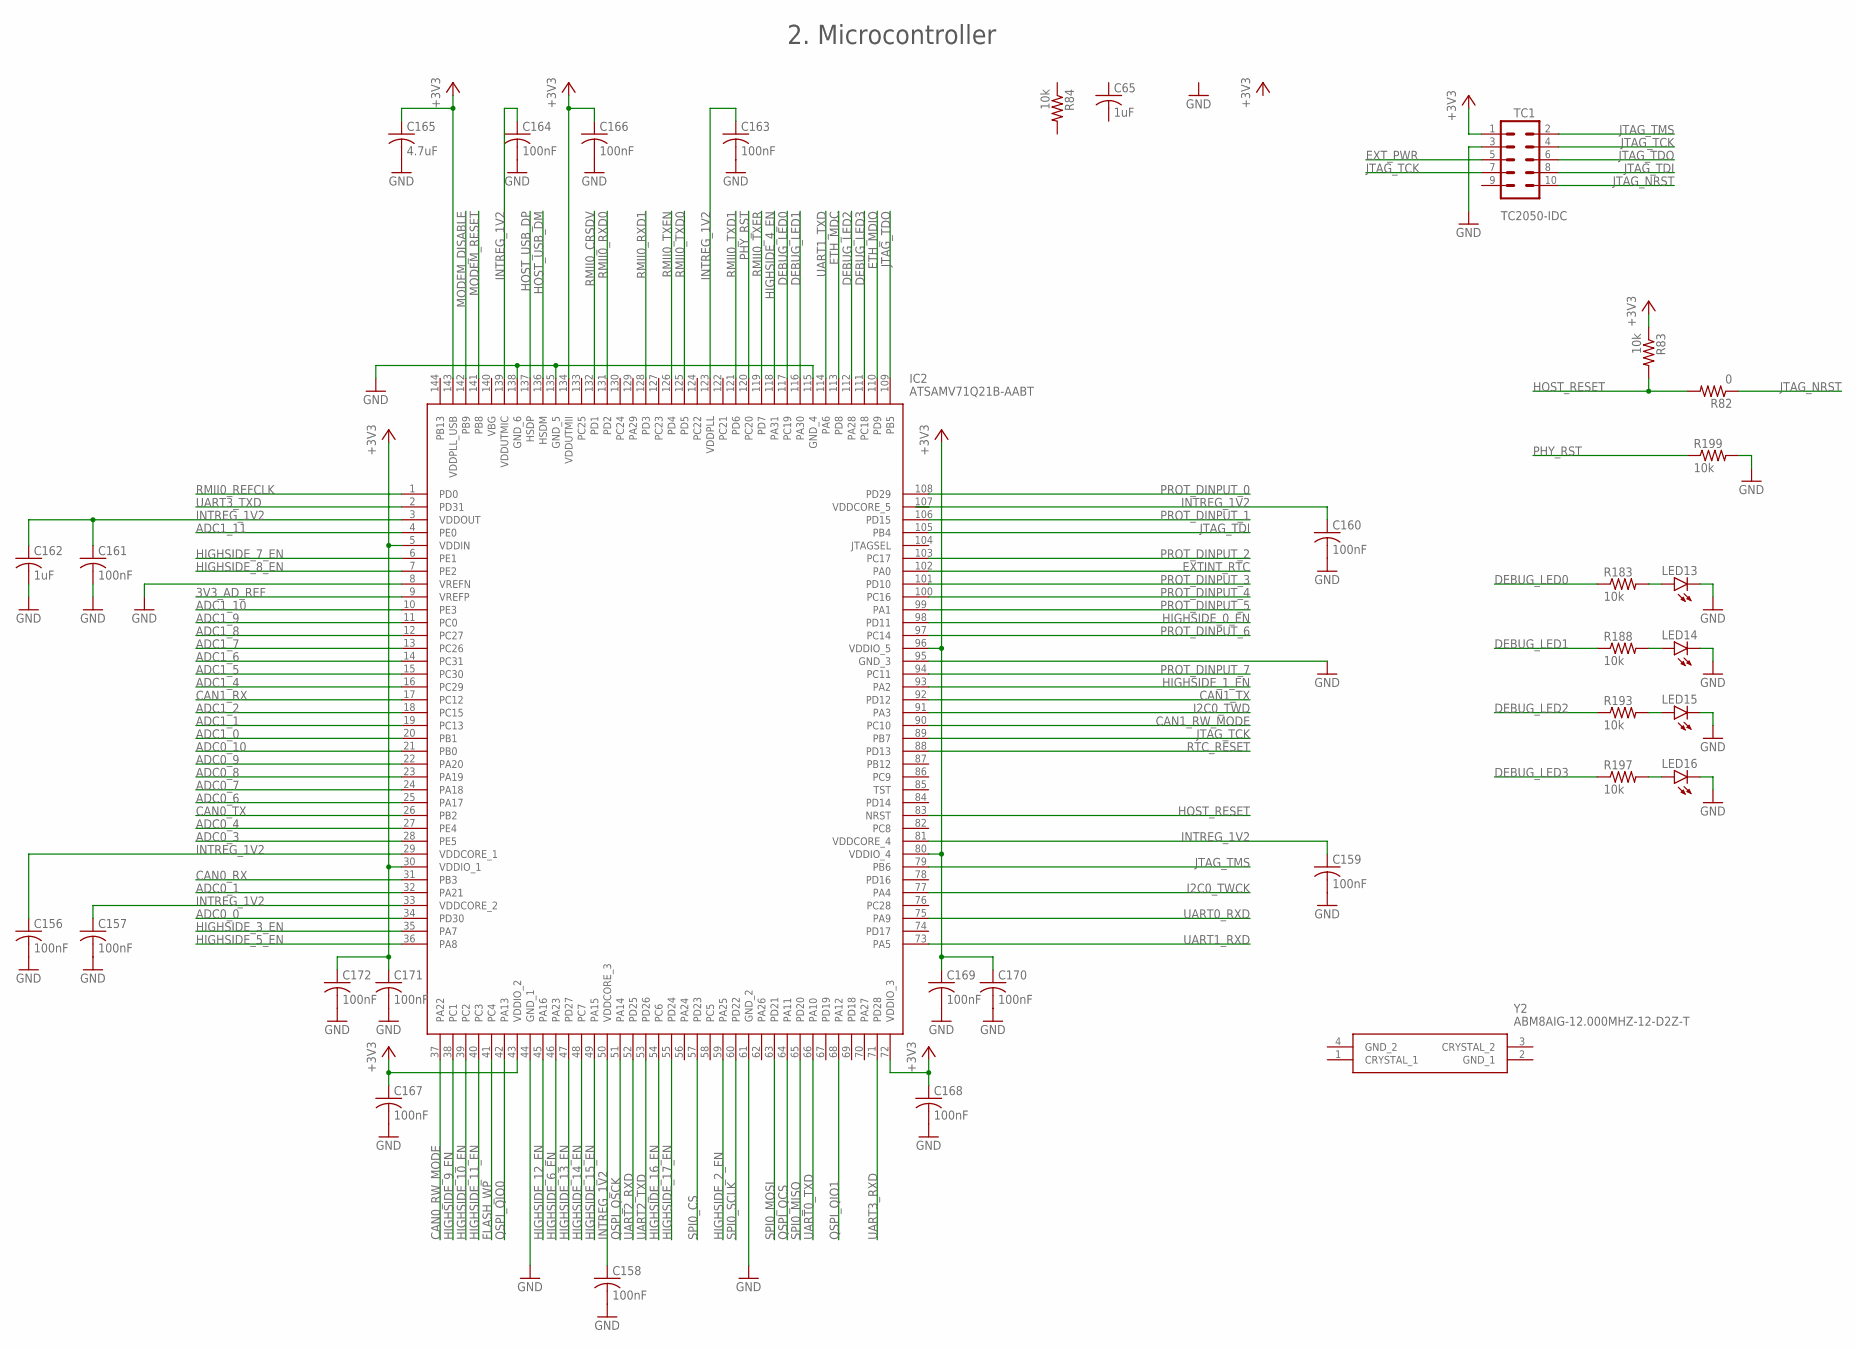
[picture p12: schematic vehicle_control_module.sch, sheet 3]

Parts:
C65, C162: 1uF; C0603
C156, C157, C158, C159, C160, C161, C163, C164, C166, C167, C168, C169, C170, C171, C172: 100nF; C0603
C165: 4.7uF; C0603
IC2: ATSAMV71Q21B-AABT; QFP50P2200X2200X160-144N
LED13, LED14, LED15, LED16: LEDCHIPLED_0603; CHIPLED_0603
R82: 0; R0603
R83, R84, R183, R188, R193, R197, R199: 10k; R0603
TC1: TC2050-IDC
Y2: ABM8AIG-12.000MHZ-12-D2Z-T; ABM8AIG12000MHZ12D2ZT

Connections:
3V3_AD_REF: IC2.9 (VREFP); also elsewhere on the board
+3V3: C165.1, C166.1, C167.1, C168.1, C169.1, C170.1, C171.1, C172.1, IC2.5 (VDDIN), IC2.30 (VDDIO_1), IC2.43 (VDDIO_2), IC2.72 (VDDIO_3), IC2.80 (VDDIO_4), IC2.96 (VDDIO_5), IC2.134 (VDDUTMII), IC2.143 (VDDPLL_USB), R83.1, TC1.1; also elsewhere on the board
ADC0_0: IC2.34 (PD30); also elsewhere on the board
ADC0_1: IC2.32 (PA21)
ADC0_3: IC2.28 (PE5); also elsewhere on the board
ADC0_4: IC2.27 (PE4); also elsewhere on the board
ADC0_6: IC2.25 (PA17); also elsewhere on the board
ADC0_7: IC2.24 (PA18); also elsewhere on the board
ADC0_8: IC2.23 (PA19); also elsewhere on the board
ADC0_9: IC2.22 (PA20); also elsewhere on the board
ADC0_10: IC2.21 (PB0); also elsewhere on the board
ADC1_0: IC2.20 (PB1); also elsewhere on the board
ADC1_1: IC2.19 (PC13); also elsewhere on the board
ADC1_2: IC2.18 (PC15); also elsewhere on the board
ADC1_4: IC2.16 (PC29); also elsewhere on the board
ADC1_5: IC2.15 (PC30); also elsewhere on the board
ADC1_6: IC2.14 (PC31); also elsewhere on the board
ADC1_7: IC2.13 (PC26); also elsewhere on the board
ADC1_8: IC2.12 (PC27); also elsewhere on the board
ADC1_9: IC2.11 (PC0); also elsewhere on the board
ADC1_10: IC2.10 (PE3); also elsewhere on the board
ADC1_11: IC2.4 (PE0); also elsewhere on the board
CAN0_RW_MODE: IC2.37 (PA22); also elsewhere on the board
CAN0_RX: IC2.31 (PB3); also elsewhere on the board
CAN0_TX: IC2.26 (PB2); also elsewhere on the board
CAN1_RW_MODE: IC2.90 (PC10); also elsewhere on the board
CAN1_RX: IC2.17 (PC12); also elsewhere on the board
CAN1_TX: IC2.92 (PD12); also elsewhere on the board
DEBUG_LED0: IC2.117 (PC19), R183.1
DEBUG_LED1: IC2.116 (PA30), R188.1
DEBUG_LED2: IC2.112 (PA28), R193.1
DEBUG_LED3: IC2.111 (PC18), R197.1
ETH_MDC: IC2.113 (PD8); also elsewhere on the board
ETH_MDIO: IC2.110 (PD9); also elsewhere on the board
EXTINT_RTC: IC2.102 (PA0); also elsewhere on the board
EXT_PWR: TC1.5; also elsewhere on the board
FLASH_WP: IC2.41 (PC4); also elsewhere on the board
GND: C156.2, C157.2, C158.2, C159.2, C160.2, C161.2, C162.2, C163.2, C164.2, C165.2, C166.2, C167.2, C168.2, C169.2, C170.2, C171.2, C172.2, IC2.8 (VREFN), IC2.44 (GND_1), IC2.61 (GND_2), IC2.95 (GND_3), IC2.115 (GND_4), IC2.135 (GND_5), IC2.138 (GND_6), LED13.C, LED14.C, LED15.C, LED16.C, R199.2, TC1.3; also elsewhere on the board
HIGHSIDE_0_EN: IC2.98 (PD11); also elsewhere on the board
HIGHSIDE_1_EN: IC2.93 (PA2); also elsewhere on the board
HIGHSIDE_2_EN: IC2.59 (PA25); also elsewhere on the board
HIGHSIDE_3_EN: IC2.35 (PA7); also elsewhere on the board
HIGHSIDE_4_EN: IC2.118 (PA31); also elsewhere on the board
HIGHSIDE_5_EN: IC2.36 (PA8); also elsewhere on the board
HIGHSIDE_6_EN: IC2.46 (PA23); also elsewhere on the board
HIGHSIDE_7_EN: IC2.6 (PE1); also elsewhere on the board
HIGHSIDE_8_EN: IC2.7 (PE2); also elsewhere on the board
HIGHSIDE_9_EN: IC2.38 (PC1); also elsewhere on the board
HIGHSIDE_10_EN: IC2.39 (PC2); also elsewhere on the board
HIGHSIDE_11_EN: IC2.40 (PC3); also elsewhere on the board
HIGHSIDE_12_EN: IC2.45 (PA16); also elsewhere on the board
HIGHSIDE_13_EN: IC2.47 (PD27); also elsewhere on the board
HIGHSIDE_14_EN: IC2.48 (PC7); also elsewhere on the board
HIGHSIDE_15_EN: IC2.49 (PA15); also elsewhere on the board
HIGHSIDE_16_EN: IC2.54 (PC6); also elsewhere on the board
HIGHSIDE_17_EN: IC2.55 (PD24); also elsewhere on the board
HOST_RESET: IC2.83 (NRST), R82.2, R83.2; also elsewhere on the board
HOST_USB_DM: IC2.136 (HSDM); also elsewhere on the board
HOST_USB_DP: IC2.137 (HSDP); also elsewhere on the board
I2C0_TWCK: IC2.77 (PA4); also elsewhere on the board
I2C0_TWD: IC2.91 (PA3); also elsewhere on the board
INTREG_1V2: C156.1, C157.1, C158.1, C159.1, C160.1, C161.1, C162.1, C163.1, C164.1, IC2.3 (VDDOUT), IC2.29 (VDDCORE_1), IC2.33 (VDDCORE_2), IC2.50 (VDDCORE_3), IC2.81 (VDDCORE_4), IC2.107 (VDDCORE_5), IC2.123 (VDDPLL), IC2.139 (VDDUTMIC)
JTAG_NRST: R82.1, TC1.10
JTAG_TCK: IC2.89 (PB7), TC1.4, TC1.7
JTAG_TDI: IC2.105 (PB4), TC1.8
JTAG_TDO: IC2.109 (PB5), TC1.6
JTAG_TMS: IC2.79 (PB6), TC1.2
MODEM_DISABLE: IC2.142 (PB9); also elsewhere on the board
MODEM_RESET: IC2.141 (PB8); also elsewhere on the board
unnamed: LED13.A, R183.2
unnamed: LED14.A, R188.2
unnamed: LED15.A, R193.2
unnamed: LED16.A, R197.2
PHY_RST: IC2.120 (PC20), R199.1; also elsewhere on the board
PROT_DINPUT_0: IC2.108 (PD29); also elsewhere on the board
PROT_DINPUT_1: IC2.106 (PD15); also elsewhere on the board
PROT_DINPUT_2: IC2.103 (PC17); also elsewhere on the board
PROT_DINPUT_3: IC2.101 (PD10); also elsewhere on the board
PROT_DINPUT_4: IC2.100 (PC16); also elsewhere on the board
PROT_DINPUT_5: IC2.99 (PA1); also elsewhere on the board
PROT_DINPUT_6: IC2.97 (PC14); also elsewhere on the board
PROT_DINPUT_7: IC2.94 (PC11); also elsewhere on the board
QSPI_QCS: IC2.64 (PA11); also elsewhere on the board
QSPI_QIO0: IC2.42 (PA13); also elsewhere on the board
QSPI_QIO1: IC2.68 (PA12); also elsewhere on the board
QSPI_QSCK: IC2.51 (PA14); also elsewhere on the board
RMII0_CRSDV: IC2.132 (PD1); also elsewhere on the board
RMII0_REFCLK: IC2.1 (PD0); also elsewhere on the board
RMII0_RXD0: IC2.131 (PD2); also elsewhere on the board
RMII0_RXD1: IC2.128 (PD3); also elsewhere on the board
RMII0_TXD0: IC2.125 (PD5); also elsewhere on the board
RMII0_TXD1: IC2.121 (PD6); also elsewhere on the board
RMII0_TXEN: IC2.126 (PD4); also elsewhere on the board
RMII0_TXER: IC2.119 (PD7); also elsewhere on the board
RTC_RESET: IC2.88 (PD13); also elsewhere on the board
SPI0_CS: IC2.57 (PD23); also elsewhere on the board
SPI0_MISO: IC2.65 (PD20); also elsewhere on the board
SPI0_MOSI: IC2.63 (PD21); also elsewhere on the board
SPI0_SCLK: IC2.60 (PD22); also elsewhere on the board
UART0_RXD: IC2.75 (PA9); also elsewhere on the board
UART0_TXD: IC2.66 (PA10); also elsewhere on the board
UART1_RXD: IC2.73 (PA5); also elsewhere on the board
UART1_TXD: IC2.114 (PA6); also elsewhere on the board
UART2_RXD: IC2.52 (PD25); also elsewhere on the board
UART2_TXD: IC2.53 (PD26); also elsewhere on the board
UART3_RXD: IC2.71 (PD28); also elsewhere on the board
UART3_TXD: IC2.2 (PD31); also elsewhere on the board

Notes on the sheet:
2. Microcontroller

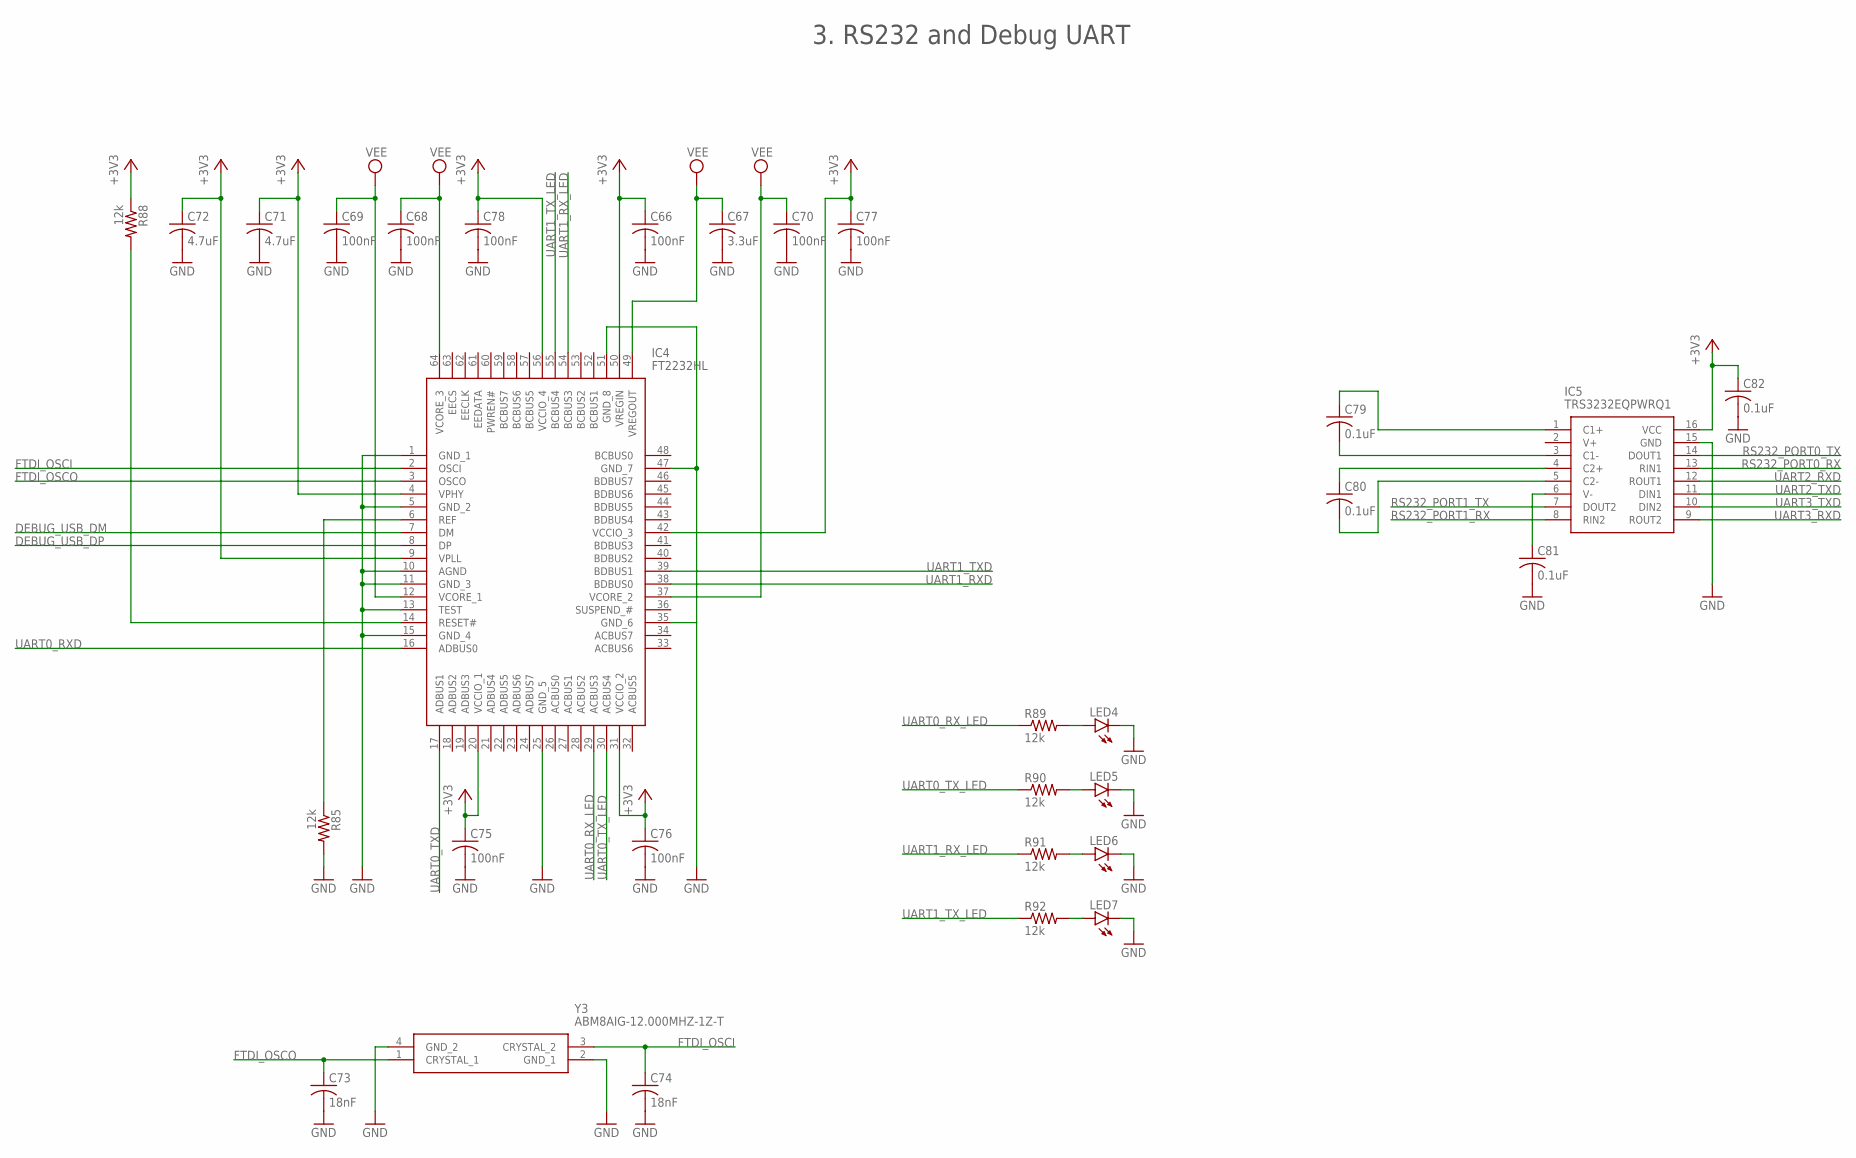
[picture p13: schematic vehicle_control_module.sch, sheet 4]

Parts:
C66, C68, C69, C70, C75, C76, C77, C78: 100nF; C0603
C67: 3.3uF; C0603
C71, C72: 4.7uF; C0603
C73, C74: 18nF; C0603
C79, C80, C81, C82: 0.1uF; C0603
IC4: FT2232HL; QFP50P1200X1200X160-64N
IC5: TRS3232EQPWRQ1; SOP65P640X120-16N
LED4, LED5, LED6, LED7: LEDCHIPLED_0603; CHIPLED_0603
R85, R88, R89, R90, R91, R92: 12k; R0603
Y3: ABM8AIG-12.000MHZ-1Z-T; ABM8AIG25000MHZ122ZT3

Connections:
+3V3: C66.1, C71.1, C72.1, C75.1, C76.1, C77.1, C78.1, C82.1, IC4.4 (VPHY), IC4.9 (VPLL), IC4.20 (VCCIO_1), IC4.31 (VCCIO_2), IC4.42 (VCCIO_3), IC4.50 (VREGIN), IC4.56 (VCCIO_4), IC5.16 (VCC), R88.1; also elsewhere on the board
DEBUG_USB_DM: IC4.7 (DM); also elsewhere on the board
DEBUG_USB_DP: IC4.8 (DP); also elsewhere on the board
FTDI_OSCI: C74.1, IC4.2 (OSCI), Y3.3 (CRYSTAL_2)
FTDI_OSCO: C73.1, IC4.3 (OSCO), Y3.1 (CRYSTAL_1)
GND: C66.2, C67.2, C68.2, C69.2, C70.2, C71.2, C72.2, C73.2, C74.2, C75.2, C76.2, C77.2, C78.2, C81.2, C82.2, IC4.1 (GND_1), IC4.5 (GND_2), IC4.10 (AGND), IC4.11 (GND_3), IC4.13 (TEST), IC4.15 (GND_4), IC4.25 (GND_5), IC4.35 (GND_6), IC4.47 (GND_7), IC4.51 (GND_8), IC5.15 (GND), LED4.C, LED5.C, LED6.C, LED7.C, R85.2, Y3.2 (GND_1), Y3.4 (GND_2); also elsewhere on the board
unnamed: IC4.6 (REF), R85.1
unnamed: IC4.14 (RESET#), R88.2
unnamed: LED5.A, R90.2
unnamed: LED4.A, R89.2
unnamed: LED6.A, R91.2
unnamed: LED7.A, R92.2
unnamed: C79.1, IC5.1 (C1+)
unnamed: C79.2, IC5.3 (C1-)
unnamed: C80.1, IC5.4 (C2+)
unnamed: C80.2, IC5.5 (C2-)
unnamed: C81.1, IC5.6 (V-)
RS232_PORT0_RX: IC5.13 (RIN1); also elsewhere on the board
RS232_PORT0_TX: IC5.14 (DOUT1); also elsewhere on the board
RS232_PORT1_RX: IC5.8 (RIN2); also elsewhere on the board
RS232_PORT1_TX: IC5.7 (DOUT2); also elsewhere on the board
UART0_RXD: IC4.16 (ADBUS0); also elsewhere on the board
UART0_RX_LED: IC4.29 (ACBUS3), R89.1
UART0_TXD: IC4.17 (ADBUS1); also elsewhere on the board
UART0_TX_LED: IC4.30 (ACBUS4), R90.1
UART1_RXD: IC4.38 (BDBUS0); also elsewhere on the board
UART1_RX_LED: IC4.54 (BCBUS3), R91.1
UART1_TXD: IC4.39 (BDBUS1); also elsewhere on the board
UART1_TX_LED: IC4.55 (BCBUS4), R92.1
UART2_RXD: IC5.12 (ROUT1); also elsewhere on the board
UART2_TXD: IC5.11 (DIN1); also elsewhere on the board
UART3_RXD: IC5.9 (ROUT2); also elsewhere on the board
UART3_TXD: IC5.10 (DIN2); also elsewhere on the board
VEE: C67.1, C68.1, C69.1, C70.1, IC4.12 (VCORE_1), IC4.37 (VCORE_2), IC4.49 (VREGOUT), IC4.64 (VCORE_3)

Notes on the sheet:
3. RS232 and Debug UART


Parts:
C64: 1uF; C0603
IC6: SST26VF032BT-104I_SM; SOIC127P794X203-8N
IC7: DS3231SN#; SOIC127P1032X265-16N
R78: 0; R0603
R79, R80, R81: 4.7k; R0603
U1: 122-2920-GR; 1222920GR

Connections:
+3V3: C64.1, IC6.7 (HOLD/SIO3), IC6.8 (VDD), IC7.2 (VCC), R78.2, R79.2, R80.2, R81.2; also elsewhere on the board
EXTINT_RTC: IC7.3 (!INT!/SQW), R81.1; also elsewhere on the board
FLASH_WP: IC6.3 (WP#/SIO2), R78.1; also elsewhere on the board
GND: C64.2, IC6.4 (VSS), IC7.5 (NC_1), IC7.6 (NC_2), IC7.7 (NC_3), IC7.8 (NC_4), IC7.9 (NC_5), IC7.10 (NC_6), IC7.11 (NC_7), IC7.12 (NC_8), IC7.13 (GND), U1.3; also elsewhere on the board
I2C0_TWCK: IC7.16 (SCL), R79.1; also elsewhere on the board
I2C0_TWD: IC7.15 (SDA), R80.1; also elsewhere on the board
unnamed: IC7.14 (VBAT), U1.1, U1.2
QSPI_QCS: IC6.1 (CE#); also elsewhere on the board
QSPI_QIO0: IC6.5 (SI/SIO0); also elsewhere on the board
QSPI_QIO1: IC6.2 (SO/SIO1); also elsewhere on the board
QSPI_QSCK: IC6.6 (SCK); also elsewhere on the board
RTC_RESET: IC7.4 (!RST); also elsewhere on the board

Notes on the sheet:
4. External Flash and RTC


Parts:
C17: 1uF; C0603
C18, C19: 8.2pF; C0603
IC1: SJA1105TELY; BGA159C80P14X14_1200X1200X150
R25: 0; R0603
Y1: NX3225SA-25MHZ-EXS00A-CS11338; NX3225SA25MHZEXS00ACS11338

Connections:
+3V3: IC1.D4 (VDDIO_MII0_1), IC1.D5 (VDDIO_MII1_1), IC1.D7 (VDDIO_MII1_2), IC1.D8 (VDDIO_MII1_3), IC1.D10 (VDDIO_MII2_1), IC1.D11 (VDDIO_MII2_2), IC1.E4 (VDDIO_MII0_2), IC1.E11 (VDDIO_MII2_3), IC1.G4 (VDDIO_MII0_3), IC1.G11 (VDDIO_MII3_1), IC1.H4 (VDDIO_CLO), IC1.K11 (VDDIO_MII3_3), IC1.L5 (VDDIO_HOST), IC1.L8 (VDDIO_MII4_1), IC1.L10 (VDDIO_MII4_2), IC1.L11 (VDDIO_MII4_3); also elsewhere on the board
GND: C18.2, C19.2, IC1.A1 (VSS_1), IC1.A14 (VSS_2), IC1.B13 (VSS_3), IC1.E5 (VSS_4), IC1.E6 (VSS_5), IC1.E7 (VSS_6), IC1.E8 (VSS_7), IC1.E9 (VSS_8), IC1.E10 (VSS_9), IC1.F5 (VSS_10), IC1.F6 (VSS_11), IC1.F7 (VSS_12), IC1.F8 (VSS_13), IC1.F9 (VSS_14), IC1.F10 (VSS_15), IC1.G5 (VSS_16), IC1.G6 (VSS_17), IC1.G7 (VSS_18), IC1.G8 (VSS_19), IC1.G9 (VSS_20), IC1.G10 (VSS_21), IC1.H5 (VSS_22), IC1.H6 (VSS_23), IC1.H7 (VSS_24), IC1.H8 (VSS_25), IC1.H9 (VSS_26), IC1.H10 (VSS_27), IC1.J2 (VSSA_PLL), IC1.J5 (VSS_28), IC1.J6 (VSS_29), IC1.J7 (VSS_30), IC1.J8 (VSS_31), IC1.J9 (VSS_32), IC1.J10 (VSS_33), IC1.K4 (VSS_34), IC1.K5 (VSS_35), IC1.K6 (VSS_36), IC1.K7 (VSS_37), IC1.K8 (VSS_38), IC1.K9 (VSS_39), IC1.K10 (VSS_40), IC1.L2 (VSSA_OSC), IC1.L7 (VSS_41), IC1.N2 (VSS_42), IC1.N13 (VSS_43), IC1.P1 (VSS_44), IC1.P14 (VSS_45), Y1.2 (GND_1), Y1.4 (GND_2); also elsewhere on the board
MII4_RXD0: IC1.N10 (MII4_RX0); also elsewhere on the board
MII4_RXD1: IC1.P11 (MII4_RX1); also elsewhere on the board
MII4_RXD2: IC1.N11 (MII4_RX2); also elsewhere on the board
MII4_RXD3: IC1.P12 (MII4_RX3); also elsewhere on the board
MII4_RX_CLK: IC1.P10 (MII4_RX_CLK); also elsewhere on the board
MII4_RX_DV: IC1.N12 (MII4_RX_DV); also elsewhere on the board
MII4_RX_ER: IC1.P13 (MII4_RX_ER)
MII4_TXD0: IC1.P7 (MII4_TXD0); also elsewhere on the board
MII4_TXD1: IC1.N7 (MII4_TXD1); also elsewhere on the board
MII4_TXD2: IC1.P8 (MII4_TXD2); also elsewhere on the board
MII4_TXD3: IC1.N8 (MII4_TXD3); also elsewhere on the board
MII4_TXEN: IC1.P9 (MII4_TXEN); also elsewhere on the board
MII4_TX_CLK: IC1.N9 (MII3_TX_ER_1); also elsewhere on the board
unnamed: C18.1, IC1.K2 (OSC_IN), Y1.1 (CRYSTAL_1)
unnamed: C19.1, IC1.L1 (OSC_OUT), Y1.3 (CRYSTAL_2)
RMII0_CRSDV: IC1.G1 (MII0_RX_DV); also elsewhere on the board
RMII0_REFCLK: IC1.D1 (MII0_TX_CLK); also elsewhere on the board
RMII0_RXD0: IC1.E1 (MII0_RX0); also elsewhere on the board
RMII0_RXD1: IC1.F2 (MII0_RX1); also elsewhere on the board
RMII0_TXD0: IC1.A2 (MII0_TXD0); also elsewhere on the board
RMII0_TXD1: IC1.B1 (MII0_TXD1); also elsewhere on the board
RMII0_TXEN: IC1.D2 (MII0_TXEN); also elsewhere on the board
RMII0_TXER: IC1.A3 (MII0_TX_ER); also elsewhere on the board
RMII1_CRSDV: IC1.A4 (MII1_RX_DV); also elsewhere on the board
RMII1_REFCLK: IC1.A7 (MII1_TX_CLK); also elsewhere on the board
RMII1_RXD0: IC1.A6 (MII1_RX0); also elsewhere on the board
RMII1_RXD1: IC1.B5 (MII1_RX1); also elsewhere on the board
RMII1_RXER: IC1.B3 (MII1_RX_ER); also elsewhere on the board
RMII1_TXD0: IC1.B9 (MII1_TXD0); also elsewhere on the board
RMII1_TXD1: IC1.A9 (MII1_TXD1); also elsewhere on the board
RMII1_TXEN: IC1.B7 (MII1_TXEN)
RMII2_CRSDV: IC1.A11 (MII2_RX_DV); also elsewhere on the board
RMII2_REFCLK: IC1.C14 (MII2_RX_CLK_2); also elsewhere on the board
RMII2_RXD0: IC1.A13 (MII2_RX0); also elsewhere on the board
RMII2_RXD1: IC1.B12 (MII2_RX1); also elsewhere on the board
RMII2_TXD0: IC1.E13 (MII2_TXD0); also elsewhere on the board
RMII2_TXD1: IC1.E14 (MII2_TXD1); also elsewhere on the board
RMII2_TXEN: IC1.C13 (MII2_TXEN)
RMII3_CRSDV: IC1.G14 (MII3_RX_DV); also elsewhere on the board
RMII3_REFCLK: IC1.K14 (MII3_TX_CLK); also elsewhere on the board
RMII3_RXD0: IC1.J14 (MII3_RX0); also elsewhere on the board
RMII3_RXD1: IC1.H13 (MII3_RX1); also elsewhere on the board
RMII3_TXD0: IC1.M13 (MII3_TXD0); also elsewhere on the board
RMII3_TXD1: IC1.M14 (MII3_TXD1); also elsewhere on the board
RMII3_TXEN: IC1.K13 (MII3_TXEN)
SPI0_CS: IC1.N6 (SS_N); also elsewhere on the board
SPI0_MISO: IC1.P4 (SDO); also elsewhere on the board
SPI0_MOSI: IC1.N5 (SDI); also elsewhere on the board
SPI0_SCLK: IC1.P5 (SCK); also elsewhere on the board
SWITCH_REF_CLK: IC1.H1 (CLK_OUT); also elsewhere on the board
VDD: IC1.D6 (VDD_CORE_1), IC1.D9 (VDD_CORE_2), IC1.F4 (VDD_CORE_3), IC1.F11 (VDD_CORE_4), IC1.J1 (VDDA_PLL), IC1.J4 (VDD_CORE_5), IC1.J11 (VDD_CORE_6), IC1.K1 (VDDA_OSC), IC1.L6 (VDD_CORE_7), IC1.L9 (VDD_CORE_8); also elsewhere on the board

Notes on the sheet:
5. Ethernet Switch

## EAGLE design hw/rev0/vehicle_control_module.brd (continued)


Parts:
C1, C3, C9: 10uF; C0603
C2, C7, C10, C11, C14, C15: 100nF; C0603
C4, C5, C8, C12: 1uF; C0603
C6, C13: 47pF; C0603
C16: 4.7nF; C0603
D1: PESD2ETH-AXR; PESD2ETHAXR
FL1: ACT45L-201-2P-TL000; ACT45L_1
FL2, FL3, FL4: BLM18PG330SN1D; BEADC1608X95N
IC3: TJA1100HNZ; QFN50P600X600X100-37N
L1, L2: 0603CS-R12XGLU; 0603CS82NXGLW
LED1: LEDCHIPLED_0603; CHIPLED_0603
R3, R19, R20, R21: 49.9; R0603
R4, R22, R23: 1k; R0603
R5, R7, R11, R14, R16, R18: 10k; R0603
R6, R8, R12, R13, R15, R17: DNP; R0603
R9: 5.11k; R0603
R10: 0; R0603
R24: 100k; R0603

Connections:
+3V3: C12.1, D1.4 (VCC), FL2.1, FL3.1, FL4.1, IC3.9 (VBAT), LED1.A, R5.2, R7.2, R9.2, R11.2, R13.2, R15.2, R17.2; also elsewhere on the board
CON_ETH1_TRX_M: C14.2, R22.2
CON_ETH1_TRX_P: C15.2, R23.2
ETH_MDC: IC3.1 (MDC); also elsewhere on the board
ETH_MDIO: IC3.36 (MDIO); also elsewhere on the board
GND: C1.2, C2.2, C3.2, C4.2, C5.2, C6.2, C7.2, C8.2, C9.2, C10.2, C11.2, C12.2, C13.2, C16.2, D1.1 (GND), IC3.15 (GND_1), IC3.20 (GND_2), IC3.26 (GND_3), IC3.34 (TXER), IC3.37 (GND_4), R6.2, R8.2, R10.1, R12.2, R14.2, R16.2, R18.2, R24.1; also elsewhere on the board
unnamed: LED1.C, R4.2
unnamed: C5.1, IC3.4 (VDDA(1V8))
unnamed: IC3.8 (WAKE/LED), R4.1
unnamed: C8.1, IC3.16 (VDDD(1V8))
unnamed: C3.1, C4.1, FL2.2, IC3.7 (VDDA(3V3))
unnamed: C1.1, C2.1, C7.1, FL3.2, IC3.11 (VDDA(TX)), IC3.14 (VDDD(3V3))
unnamed: C9.1, C10.1, C11.1, FL4.2, IC3.19 (VDD(IO)_1), IC3.27 (VDD(IO)_2)
unnamed: IC3.35 (EN), R9.1
unnamed: IC3.6 (XI), R10.2
unnamed: D1.3 (I/O_2), FL1.1, L2.2, R21.2
unnamed: D1.2 (I/O_1), FL1.2, L1.2, R19.2
unnamed: C6.1, R3.2, R19.1
unnamed: C13.1, R20.2, R21.1
unnamed: C14.1, FL1.4
unnamed: C15.1, FL1.3
unnamed: C16.1, R22.1, R23.1, R24.2
PHY1_CONFIG0: IC3.22 (RXD2/CONFIG0), R5.1, R6.1
PHY1_CONFIG1: IC3.21 (RXD3/CONFIG1), R7.1, R8.1
PHY1_TRX_M: IC3.13 (TRX_M), L2.1, R20.1
PHY1_TRX_P: IC3.12 (TRX_P), L1.1, R3.1
PHY_RST: IC3.3 (RST_N); also elsewhere on the board
RMII1_CRSDV: IC3.18 (RXDV/CONFIG2/CRSDV), R11.1, R12.1; also elsewhere on the board
RMII1_REFCLK: IC3.25 (RXC/REF_CLK); also elsewhere on the board
RMII1_RXD0: IC3.24 (RXD0/PHYAD0), R15.1, R16.1; also elsewhere on the board
RMII1_RXD1: IC3.23 (RXD1/PHYAD1), R17.1, R18.1; also elsewhere on the board
RMII1_RXER: IC3.17 (RXER/CONFIG3), R13.1, R14.1; also elsewhere on the board
RMII1_TXD0: IC3.33 (TXD0); also elsewhere on the board
RMII1_TXD1: IC3.32 (TXD1); also elsewhere on the board

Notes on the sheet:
Place close to pin 7
Place close to pin 9
Place close to pin 14
Place close to pin 19, 27
CONFIG0: 0 = PHY is configured as Slave 1 = PHY is configured as Master
CONFIG1: 0 = Managed operation 1 = Autonomous operation
Note the pin swap!
6. Ethernet PHY 1


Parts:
C32, C34, C39: 10uF; C0603
C33, C37, C40, C41, C45, C46: 100nF; C0603
C35, C36, C38, C42: 1uF; C0603
C43, C44: 47pF; C0603
C47: 4.7nF; C0603
D2: PESD2ETH-AXR; PESD2ETHAXR
FL5: ACT45L-201-2P-TL000; ACT45L_1
FL6, FL7, FL8: BLM18PG330SN1D; BEADC1608X95N
IC10: TJA1100HNZ; QFN50P600X600X100-37N
L3, L4: 0603CS-R12XGLU; 0603CS82NXGLW
LED2: LEDCHIPLED_0603; CHIPLED_0603
R34, R50, R51, R52: 49.9; R0603
R35, R53, R54: 1k; R0603
R36, R38, R42, R45, R47, R49: 10k; R0603
R37, R39, R43, R44, R46, R48: DNP; R0603
R40: 5.11k; R0603
R41: 0; R0603
R55: 100k; R0603

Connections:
+3V3: C42.1, D2.4 (VCC), FL6.1, FL7.1, FL8.1, IC10.9 (VBAT), LED2.A, R36.2, R38.2, R40.2, R42.2, R44.2, R46.2, R48.2; also elsewhere on the board
CON_ETH2_TRX_M: C45.2, R53.2
CON_ETH2_TRX_P: C46.2, R54.2
ETH_MDC: IC10.1 (MDC); also elsewhere on the board
ETH_MDIO: IC10.36 (MDIO); also elsewhere on the board
GND: C32.2, C33.2, C34.2, C35.2, C36.2, C37.2, C38.2, C39.2, C40.2, C41.2, C42.2, C43.2, C44.2, C47.2, D2.1 (GND), IC10.15 (GND_1), IC10.20 (GND_2), IC10.26 (GND_3), IC10.34 (TXER), IC10.37 (GND_4), R37.2, R39.2, R41.1, R43.2, R45.2, R47.2, R49.2, R55.1; also elsewhere on the board
unnamed: LED2.C, R35.2
unnamed: IC10.8 (WAKE/LED), R35.1
unnamed: C36.1, IC10.4 (VDDA(1V8))
unnamed: C38.1, IC10.16 (VDDD(1V8))
unnamed: C34.1, C35.1, FL6.2, IC10.7 (VDDA(3V3))
unnamed: C32.1, C33.1, C37.1, FL7.2, IC10.11 (VDDA(TX)), IC10.14 (VDDD(3V3))
unnamed: C39.1, C40.1, C41.1, FL8.2, IC10.19 (VDD(IO)_1), IC10.27 (VDD(IO)_2)
unnamed: IC10.35 (EN), R40.1
unnamed: IC10.6 (XI), R41.2
unnamed: D2.3 (I/O_2), FL5.1, L4.2, R52.2
unnamed: D2.2 (I/O_1), FL5.2, L3.2, R50.2
unnamed: C43.1, R34.2, R50.1
unnamed: C44.1, R51.2, R52.1
unnamed: C45.1, FL5.4
unnamed: C46.1, FL5.3
unnamed: C47.1, R53.1, R54.1, R55.2
PHY2_CONFIG0: IC10.22 (RXD2/CONFIG0), R36.1, R37.1
PHY2_CONFIG1: IC10.21 (RXD3/CONFIG1), R38.1, R39.1
PHY2_TRX_M: IC10.13 (TRX_M), L4.1, R51.1
PHY2_TRX_P: IC10.12 (TRX_P), L3.1, R34.1
PHY_RST: IC10.3 (RST_N); also elsewhere on the board
RMII2_CRSDV: IC10.18 (RXDV/CONFIG2/CRSDV), R42.1, R43.1; also elsewhere on the board
RMII2_REFCLK: IC10.25 (RXC/REF_CLK); also elsewhere on the board
RMII2_RXD0: IC10.24 (RXD0/PHYAD0), R46.1, R47.1; also elsewhere on the board
RMII2_RXD1: IC10.23 (RXD1/PHYAD1), R48.1, R49.1; also elsewhere on the board
RMII2_RXER: IC10.17 (RXER/CONFIG3), R44.1, R45.1
RMII2_TXD0: IC10.33 (TXD0); also elsewhere on the board
RMII2_TXD1: IC10.32 (TXD1); also elsewhere on the board

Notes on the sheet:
Place close to pin 7
Place close to pin 9
Place close to pin 14
Place close to pin 19, 27
CONFIG0: 0 = PHY is configured as Slave 1 = PHY is configured as Master
CONFIG1: 0 = Managed operation 1 = Autonomous operation
Note the pin swap!
7. Ethernet PHY 2

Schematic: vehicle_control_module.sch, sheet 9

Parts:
C48, C50, C55: 10uF; C0603
C49, C53, C56, C57, C61, C62: 100nF; C0603
C51, C52, C54, C58: 1uF; C0603
C59, C60: 47pF; C0603
C63: 4.7nF; C0603
D3: PESD2ETH-AXR; PESD2ETHAXR
FL9: ACT45L-201-2P-TL000; ACT45L_1
FL10, FL11, FL12: BLM18PG330SN1D; BEADC1608X95N
IC12: TJA1100HNZ; QFN50P600X600X100-37N
L5, L6: 0603CS-R12XGLU; 0603CS82NXGLW
LED3: LEDCHIPLED_0603; CHIPLED_0603
R56, R72, R73, R74: 49.9; R0603
R57, R75, R76: 1k; R0603
R58, R60, R64, R67, R69, R71: 10k; R0603
R59, R61, R65, R66, R68, R70: DNP; R0603
R62: 5.11k; R0603
R63: 0; R0603
R77: 100k; R0603

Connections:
+3V3: C58.1, D3.4 (VCC), FL10.1, FL11.1, FL12.1, IC12.9 (VBAT), LED3.A, R58.2, R60.2, R62.2, R64.2, R66.2, R68.2, R70.2; also elsewhere on the board
CON_ETH3_TRX_M: C61.2, R75.2
CON_ETH3_TRX_P: C62.2, R76.2
ETH_MDC: IC12.1 (MDC); also elsewhere on the board
ETH_MDIO: IC12.36 (MDIO); also elsewhere on the board
GND: C48.2, C49.2, C50.2, C51.2, C52.2, C53.2, C54.2, C55.2, C56.2, C57.2, C58.2, C59.2, C60.2, C63.2, D3.1 (GND), IC12.15 (GND_1), IC12.20 (GND_2), IC12.26 (GND_3), IC12.34 (TXER), IC12.37 (GND_4), R59.2, R61.2, R63.1, R65.2, R67.2, R69.2, R71.2, R77.1; also elsewhere on the board
unnamed: LED3.C, R57.2
unnamed: IC12.8 (WAKE/LED), R57.1
unnamed: C52.1, IC12.4 (VDDA(1V8))
unnamed: C54.1, IC12.16 (VDDD(1V8))
unnamed: C50.1, C51.1, FL10.2, IC12.7 (VDDA(3V3))
unnamed: C48.1, C49.1, C53.1, FL11.2, IC12.11 (VDDA(TX)), IC12.14 (VDDD(3V3))
unnamed: C55.1, C56.1, C57.1, FL12.2, IC12.19 (VDD(IO)_1), IC12.27 (VDD(IO)_2)
unnamed: IC12.35 (EN), R62.1
unnamed: IC12.6 (XI), R63.2
unnamed: D3.3 (I/O_2), FL9.1, L6.2, R74.2
unnamed: D3.2 (I/O_1), FL9.2, L5.2, R72.2
unnamed: C59.1, R56.2, R72.1
unnamed: C60.1, R73.2, R74.1
unnamed: C61.1, FL9.4
unnamed: C62.1, FL9.3
unnamed: C63.1, R75.1, R76.1, R77.2
PHY3_CONFIG0: IC12.22 (RXD2/CONFIG0), R58.1, R59.1
PHY3_CONFIG1: IC12.21 (RXD3/CONFIG1), R60.1, R61.1
PHY3_TRX_M: IC12.13 (TRX_M), L6.1, R73.1
PHY3_TRX_P: IC12.12 (TRX_P), L5.1, R56.1
PHY_RST: IC12.3 (RST_N); also elsewhere on the board
RMII3_CRSDV: IC12.18 (RXDV/CONFIG2/CRSDV), R64.1, R65.1; also elsewhere on the board
RMII3_REFCLK: IC12.25 (RXC/REF_CLK); also elsewhere on the board
RMII3_RXD0: IC12.24 (RXD0/PHYAD0), R68.1, R69.1; also elsewhere on the board
RMII3_RXD1: IC12.23 (RXD1/PHYAD1), R70.1, R71.1; also elsewhere on the board
RMII3_RXER: IC12.17 (RXER/CONFIG3), R66.1, R67.1
RMII3_TXD0: IC12.33 (TXD0); also elsewhere on the board
RMII3_TXD1: IC12.32 (TXD1); also elsewhere on the board

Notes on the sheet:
Place close to pin 7
Place close to pin 9
Place close to pin 14
Place close to pin 19, 27
CONFIG0: 0 = PHY is configured as Slave 1 = PHY is configured as Master
CONFIG1: 0 = Managed operation 1 = Autonomous operation
Note the pin swap!
8. Ethernet PHY 3

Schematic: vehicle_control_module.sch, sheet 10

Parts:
C23, C25, C28: 10uF; C0603
C24, C26, C27, C29: 0.1uF; C0603
IC11: KSZ8061MNXI-TR; QFN50P500X500X85-33N
R31: 6.04k; R0603
R32: 4.7k; R0603

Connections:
+3V3: C23.1, C24.1, IC11.3 (AVDDH), IC11.15 (VDDIO), R32.1; also elsewhere on the board
DEBUG_ETH_CONFIG1: IC11.27 (CRS), R32.2
DEBUG_ETH_LED0: IC11.24 (LED0/TXER); also elsewhere on the board
DEBUG_ETH_LED1: IC11.32 (SIGDET); also elsewhere on the board
DEBUG_ETH_RXM: IC11.7 (RXM); also elsewhere on the board
DEBUG_ETH_RXP: IC11.6 (RXP); also elsewhere on the board
DEBUG_ETH_TXM: IC11.5 (TXM); also elsewhere on the board
DEBUG_ETH_TXP: IC11.4 (TXP); also elsewhere on the board
ETH_MDC: IC11.11 (MDC); also elsewhere on the board
ETH_MDIO: IC11.10 (MDIO); also elsewhere on the board
GND: C23.2, C24.2, C25.2, C26.2, C27.2, C28.2, C29.2, IC11.33 (PADDLE), R31.1; also elsewhere on the board
MII4_RXD0: IC11.18 (RXD0); also elsewhere on the board
MII4_RXD1: IC11.17 (RXD1); also elsewhere on the board
MII4_RXD2: IC11.16 (RXD2); also elsewhere on the board
MII4_RXD3: IC11.14 (RXD3); also elsewhere on the board
MII4_RXERR: IC11.12 (RXERR)
MII4_RX_CLK: IC11.19 (RXC); also elsewhere on the board
MII4_RX_DV: IC11.13 (RXDV); also elsewhere on the board
MII4_TXD0: IC11.22 (TXD0); also elsewhere on the board
MII4_TXD1: IC11.23 (TXD1); also elsewhere on the board
MII4_TXD2: IC11.25 (TXD2); also elsewhere on the board
MII4_TXD3: IC11.26 (TXD3); also elsewhere on the board
MII4_TXEN: IC11.21 (TXEN); also elsewhere on the board
MII4_TX_CLK: IC11.20 (TXC); also elsewhere on the board
unnamed: IC11.31 (REXT), R31.2
PHY_RESET: IC11.28 (!RESET)
SWITCH_REF_CLK: IC11.1 (XI); also elsewhere on the board
VDD: C25.1, C26.1, C27.1, C28.1, C29.1, IC11.8 (AVDDL), IC11.9 (VDDL_1), IC11.30 (VDDL_2); also elsewhere on the board

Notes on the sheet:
9. Ethernet PHY 4

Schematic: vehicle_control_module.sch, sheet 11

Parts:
C128, C130, C132, C134, C136, C138, C140, C142, C144: 0.01uF; C0603
C129, C131, C133, C135, C137, C139, C141, C143, C145: 150nF; C0603
D19, D20, D21, D22, D23, D24, D25, D26, D27: BAT54SWFILMY; SOT65P210X110-3N
R150, R155, R160, R165, R170, R175, R180, R185, R190: 4; R1206
R151, R154, R156, R159, R161, R164, R166, R169, R171, R174, R176, R179, R181, R184, R186, R189, R191, R194: 4.7k; R0603
R152, R157, R162, R167, R172, R177, R182, R187, R192: 2.74k; R0603
U?10, U?11, U?12, U?13, U?14, U?15, U?16, U?17, U?18: BTS50015-1TAD; TO127P1500X450-7_8N-V1

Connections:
+3V3: D19.2 (K), D20.2 (K), D21.2 (K), D22.2 (K), D23.2 (K), D24.2 (K), D25.2 (K), D26.2 (K), D27.2 (K); also elsewhere on the board
ADC0_3: C128.1, D19.3 (A,K), R151.2; also elsewhere on the board
ADC0_4: C130.1, D20.3 (A,K), R156.2; also elsewhere on the board
ADC0_6: C132.1, D21.3 (A,K), R161.2; also elsewhere on the board
ADC0_7: C134.1, D22.3 (A,K), R166.2; also elsewhere on the board
ADC0_8: C136.1, D23.3 (A,K), R171.2; also elsewhere on the board
ADC0_9: C138.1, D24.3 (A,K), R176.2; also elsewhere on the board
ADC0_10: C140.1, D25.3 (A,K), R181.2; also elsewhere on the board
ADC1_0: C142.1, D26.3 (A,K), R186.2; also elsewhere on the board
ADC1_1: C144.1, D27.3 (A,K), R191.2; also elsewhere on the board
GND: C128.2, C130.2, C132.2, C134.2, C136.2, C138.2, C140.2, C142.2, C144.2, D19.1 (A), D20.1 (A), D21.1 (A), D22.1 (A), D23.1 (A), D24.1 (A), D25.1 (A), D26.1 (A), D27.1 (A), R150.2, R152.2, R155.2, R157.2, R160.2, R162.2, R165.2, R167.2, R170.2, R172.2, R175.2, R177.2, R180.2, R182.2, R185.2, R187.2, R190.2, R192.2; also elsewhere on the board
HIGHSIDE_0_EN: R154.2; also elsewhere on the board
HIGHSIDE_0_OUTPUT: U?10.5 (OUT1), U?10.6 (OUT2), U?10.7 (OUT3)
HIGHSIDE_1_EN: R159.2; also elsewhere on the board
HIGHSIDE_1_OUTPUT: U?11.5 (OUT1), U?11.6 (OUT2), U?11.7 (OUT3)
HIGHSIDE_2_EN: R164.2; also elsewhere on the board
HIGHSIDE_2_OUTPUT: U?12.5 (OUT1), U?12.6 (OUT2), U?12.7 (OUT3)
HIGHSIDE_3_EN: R169.2; also elsewhere on the board
HIGHSIDE_3_OUTPUT: U?13.5 (OUT1), U?13.6 (OUT2), U?13.7 (OUT3)
HIGHSIDE_4_EN: R174.2; also elsewhere on the board
HIGHSIDE_4_OUTPUT: U?14.5 (OUT1), U?14.6 (OUT2), U?14.7 (OUT3)
HIGHSIDE_5_EN: R179.2; also elsewhere on the board
HIGHSIDE_5_OUTPUT: U?15.5 (OUT1), U?15.6 (OUT2), U?15.7 (OUT3)
HIGHSIDE_6_EN: R184.2; also elsewhere on the board
HIGHSIDE_6_OUTPUT: U?16.5 (OUT1), U?16.6 (OUT2), U?16.7 (OUT3)
HIGHSIDE_7_EN: R189.2; also elsewhere on the board
HIGHSIDE_7_OUTPUT: U?17.5 (OUT1), U?17.6 (OUT2), U?17.7 (OUT3)
HIGHSIDE_8_EN: R194.2; also elsewhere on the board
HIGHSIDE_8_OUTPUT: U?18.5 (OUT1), U?18.6 (OUT2), U?18.7 (OUT3)
unnamed: C129.2, R150.1, U?10.1 (GND)
unnamed: R151.1, R152.1, U?10.3 (IS)
unnamed: C129.1, R154.1, U?10.2 (IN)
unnamed: C131.2, R155.1, U?11.1 (GND)
unnamed: R156.1, R157.1, U?11.3 (IS)
unnamed: C131.1, R159.1, U?11.2 (IN)
unnamed: C133.2, R160.1, U?12.1 (GND)
unnamed: R161.1, R162.1, U?12.3 (IS)
unnamed: C133.1, R164.1, U?12.2 (IN)
unnamed: C135.2, R165.1, U?13.1 (GND)
unnamed: R166.1, R167.1, U?13.3 (IS)
unnamed: C135.1, R169.1, U?13.2 (IN)
unnamed: C137.2, R170.1, U?14.1 (GND)
unnamed: R171.1, R172.1, U?14.3 (IS)
unnamed: C137.1, R174.1, U?14.2 (IN)
unnamed: C139.2, R175.1, U?15.1 (GND)
unnamed: R176.1, R177.1, U?15.3 (IS)
unnamed: C139.1, R179.1, U?15.2 (IN)
unnamed: C141.2, R180.1, U?16.1 (GND)
unnamed: R181.1, R182.1, U?16.3 (IS)
unnamed: C141.1, R184.1, U?16.2 (IN)
unnamed: C143.2, R185.1, U?17.1 (GND)
unnamed: R186.1, R187.1, U?17.3 (IS)
unnamed: C143.1, R189.1, U?17.2 (IN)
unnamed: C145.2, R190.1, U?18.1 (GND)
unnamed: R191.1, R192.1, U?18.3 (IS)
unnamed: C145.1, R194.1, U?18.2 (IN)
VBATT: U?10.8 (VS), U?11.8 (VS), U?12.8 (VS), U?13.8 (VS), U?14.8 (VS), U?15.8 (VS), U?16.8 (VS), U?17.8 (VS), U?18.8 (VS); also elsewhere on the board

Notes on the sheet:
10. High Side Drivers (1/2)
RC lowpass on IS results in ~3400Hz cutoff

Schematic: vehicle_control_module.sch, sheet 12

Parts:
C108, C111, C114, C116, C118, C120, C122, C124, C126: 0.01uF; C0603
C112, C113, C115, C117, C119, C121, C123, C125, C127: 150nF; C0603
D10, D11, D12, D13, D14, D15, D16, D17, D18: BAT54SWFILMY; SOT65P210X110-3N
R105, R106, R115, R120, R125, R130, R135, R140, R145: 4; R1206
R107, R110, R111, R114, R116, R119, R121, R124, R126, R129, R131, R134, R136, R139, R141, R144, R146, R149: 4.7k; R0603
R108, R112, R117, R122, R127, R132, R137, R142, R147: 2.74k; R0603
U?1, U?2, U?3, U?4, U?5, U?6, U?7, U?8, U?9: BTS50015-1TAD; TO127P1500X450-7_8N-V1

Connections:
+3V3: D10.2 (K), D11.2 (K), D12.2 (K), D13.2 (K), D14.2 (K), D15.2 (K), D16.2 (K), D17.2 (K), D18.2 (K); also elsewhere on the board
ADC1_2: C111.1, D10.3 (A,K), R107.2; also elsewhere on the board
ADC1_4: C108.1, D11.3 (A,K), R111.2; also elsewhere on the board
ADC1_5: C114.1, D12.3 (A,K), R116.2; also elsewhere on the board
ADC1_6: C116.1, D13.3 (A,K), R121.2; also elsewhere on the board
ADC1_7: C118.1, D14.3 (A,K), R126.2; also elsewhere on the board
ADC1_8: C120.1, D15.3 (A,K), R131.2; also elsewhere on the board
ADC1_9: C122.1, D16.3 (A,K), R136.2; also elsewhere on the board
ADC1_10: C124.1, D17.3 (A,K), R141.2; also elsewhere on the board
ADC1_11: C126.1, D18.3 (A,K), R146.2; also elsewhere on the board
GND: C108.2, C111.2, C114.2, C116.2, C118.2, C120.2, C122.2, C124.2, C126.2, D10.1 (A), D11.1 (A), D12.1 (A), D13.1 (A), D14.1 (A), D15.1 (A), D16.1 (A), D17.1 (A), D18.1 (A), R105.2, R106.2, R108.2, R112.2, R115.2, R117.2, R120.2, R122.2, R125.2, R127.2, R130.2, R132.2, R135.2, R137.2, R140.2, R142.2, R145.2, R147.2; also elsewhere on the board
HIGHSIDE_9_EN: R110.2; also elsewhere on the board
HIGHSIDE_9_OUTPUT: U?1.5 (OUT1), U?1.6 (OUT2), U?1.7 (OUT3)
HIGHSIDE_10_EN: R114.2; also elsewhere on the board
HIGHSIDE_10_OUTPUT: U?2.5 (OUT1), U?2.6 (OUT2), U?2.7 (OUT3)
HIGHSIDE_11_EN: R119.2; also elsewhere on the board
HIGHSIDE_11_OUTPUT: U?3.5 (OUT1), U?3.6 (OUT2), U?3.7 (OUT3)
HIGHSIDE_12_EN: R124.2; also elsewhere on the board
HIGHSIDE_12_OUTPUT: U?4.5 (OUT1), U?4.6 (OUT2), U?4.7 (OUT3)
HIGHSIDE_13_EN: R129.2; also elsewhere on the board
HIGHSIDE_13_OUTPUT: U?5.5 (OUT1), U?5.6 (OUT2), U?5.7 (OUT3)
HIGHSIDE_14_EN: R134.2; also elsewhere on the board
HIGHSIDE_14_OUTPUT: U?6.5 (OUT1), U?6.6 (OUT2), U?6.7 (OUT3)
HIGHSIDE_15_EN: R139.2; also elsewhere on the board
HIGHSIDE_15_OUTPUT: U?7.5 (OUT1), U?7.6 (OUT2), U?7.7 (OUT3)
HIGHSIDE_16_EN: R144.2; also elsewhere on the board
HIGHSIDE_16_OUTPUT: U?8.5 (OUT1), U?8.6 (OUT2), U?8.7 (OUT3)
HIGHSIDE_17_EN: R149.2; also elsewhere on the board
HIGHSIDE_17_OUTPUT: U?9.5 (OUT1), U?9.6 (OUT2), U?9.7 (OUT3)
unnamed: C112.2, R106.1, U?1.1 (GND)
unnamed: R107.1, R108.1, U?1.3 (IS)
unnamed: C113.2, R105.1, U?2.1 (GND)
unnamed: C112.1, R110.1, U?1.2 (IN)
unnamed: R111.1, R112.1, U?2.3 (IS)
unnamed: C113.1, R114.1, U?2.2 (IN)
unnamed: C115.2, R115.1, U?3.1 (GND)
unnamed: R116.1, R117.1, U?3.3 (IS)
unnamed: C115.1, R119.1, U?3.2 (IN)
unnamed: C117.2, R120.1, U?4.1 (GND)
unnamed: R121.1, R122.1, U?4.3 (IS)
unnamed: C117.1, R124.1, U?4.2 (IN)
unnamed: C119.2, R125.1, U?5.1 (GND)
unnamed: R126.1, R127.1, U?5.3 (IS)
unnamed: C119.1, R129.1, U?5.2 (IN)
unnamed: C121.2, R130.1, U?6.1 (GND)
unnamed: R131.1, R132.1, U?6.3 (IS)
unnamed: C121.1, R134.1, U?6.2 (IN)
unnamed: C123.2, R135.1, U?7.1 (GND)
unnamed: R136.1, R137.1, U?7.3 (IS)
unnamed: C123.1, R139.1, U?7.2 (IN)
unnamed: C125.2, R140.1, U?8.1 (GND)
unnamed: R141.1, R142.1, U?8.3 (IS)
unnamed: C125.1, R144.1, U?8.2 (IN)
unnamed: C127.2, R145.1, U?9.1 (GND)
unnamed: R146.1, R147.1, U?9.3 (IS)
unnamed: C127.1, R149.1, U?9.2 (IN)
VBATT: U?1.8 (VS), U?2.8 (VS), U?3.8 (VS), U?4.8 (VS), U?5.8 (VS), U?6.8 (VS), U?7.8 (VS), U?8.8 (VS), U?9.8 (VS); also elsewhere on the board

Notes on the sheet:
11. High Side Drivers (2/2)
RC lowpass on IS results in ~3400Hz cutoff

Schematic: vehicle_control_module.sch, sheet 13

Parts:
C90, C93: 4.7nF; C0603
C91, C94, C146, C147: 100nF; C0603
C92, C95: 10uF; C0603
IC13, IC18: TLE9250XSJXUMA1; SOIC127P602X173-8N
R1, R2, R95, R96: 60; R0805
R195, R196: 10k; R0603

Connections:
+3V3: C146.1, C147.1, IC13.5 (VIO), IC18.5 (VIO), R195.1, R196.1; also elsewhere on the board
+5V: C91.1, C92.1, C94.1, C95.1, IC13.3 (VCC), IC18.3 (VCC); also elsewhere on the board
CAN0_H: IC13.7 (CANH), R1.1
CAN0_L: IC13.6 (CANL), R2.2
CAN0_RW_MODE: IC13.8 (RM), R196.2; also elsewhere on the board
CAN0_RX: IC13.4 (RXD); also elsewhere on the board
CAN0_TX: IC13.1 (TXD); also elsewhere on the board
CAN1_H: IC18.7 (CANH), R95.1
CAN1_L: IC18.6 (CANL), R96.2
CAN1_RW_MODE: IC18.8 (RM), R195.2; also elsewhere on the board
CAN1_RX: IC18.4 (RXD); also elsewhere on the board
CAN1_TX: IC18.1 (TXD); also elsewhere on the board
GND: C90.2, C91.2, C92.2, C93.2, C94.2, C95.2, C146.2, C147.2, IC13.2 (GND), IC18.2 (GND); also elsewhere on the board
unnamed: C93.1, R95.2, R96.1
unnamed: C90.1, R1.2, R2.1

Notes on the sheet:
12. CAN

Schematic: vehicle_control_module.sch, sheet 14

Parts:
C96: 1uF; C0603
C97: UCZ1K151MNQ1MS; CAPAE1360X1450N
C98: 100nF; C0603
J15: 693022010811
J27: 2041119-2; 20411192
LED9: LEDCHIPLED_0603; CHIPLED_0603
R102: 10k; R0603

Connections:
+3V3: C96.1, C97.1 (+), C98.1, J27.2 (3.3VAUX), J27.24 (+3.3VAUX_1), J27.39 (+3.3VAUX_2), J27.41 (+3.3VAUX_3), J27.52 (+3.3VAUX_4), R102.1; also elsewhere on the board
GND: C96.2, C97.2 (-), C98.2, J15.5 (GND), J27.4 (GND_1), J27.9 (GND_2), J27.15 (GND_3), J27.18 (GND_4), J27.21 (GND_5), J27.26 (GND_6), J27.27 (GND_7), J27.29 (GND_8), J27.34 (GND_9), J27.35 (GND_10), J27.37 (GND_11), J27.40 (GND_12), J27.43 (GND_13), J27.45 (RESERVED_1), J27.50 (GND_14); also elsewhere on the board
HOST_USB_DM: J27.36 (USB_D-); also elsewhere on the board
HOST_USB_DP: J27.38 (USB_D+); also elsewhere on the board
MODEM_DISABLE: J27.20 (W_DISABLE#); also elsewhere on the board
MODEM_RESET: J27.22 (PERST#); also elsewhere on the board
MODEM_WAN_LED: J27.42 (LED_WWAN#), LED9.C
unnamed: LED9.A, R102.2
SIM_CLK: J15.3 (CLK), J27.12 (UIM_CLK)
SIM_DATA: J15.7 (I/O), J27.10 (UIM_DATA)
SIM_PWR: J15.1 (VCC), J15.6 (VPP), J27.8 (UIM_PWR)
SIM_RESET: J15.2 (RST), J27.14 (UIM_RESET)

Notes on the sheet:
13. Modem
MicroSIM socket

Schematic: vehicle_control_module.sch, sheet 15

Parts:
C148, C149, C150, C151, C152, C153, C154, C155: 0.01uF; C0603
D28, D29, D30, D31, D32, D33, D34, D35: BAT54SWFILMY; SOT65P210X110-3N
IC8: 74HC7541D-Q100J; SOIC127P1032X265-20N
R109, R118, R128, R138, R148, R158, R168, R178: 100k; R0603
R113, R123, R133, R143, R153, R163, R173, R198: 4.7k; R0603

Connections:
+3V3: D28.1 (A), D29.1 (A), D30.1 (A), D31.1 (A), D32.1 (A), D33.1 (A), D34.1 (A), D35.1 (A), IC8.20 (VCC); also elsewhere on the board
EXT_DINPUT_0: R198.1
EXT_DINPUT_1: R113.1
EXT_DINPUT_2: R123.1
EXT_DINPUT_3: R133.1
EXT_DINPUT_4: R143.1
EXT_DINPUT_5: R153.1
EXT_DINPUT_6: R163.1
EXT_DINPUT_7: R173.1
GND: C148.2, C149.2, C150.2, C151.2, C152.2, C153.2, C154.2, C155.2, D28.2 (K), D29.2 (K), D30.2 (K), D31.2 (K), D32.2 (K), D33.2 (K), D34.2 (K), D35.2 (K), IC8.1 (!OE1), IC8.10 (GND), IC8.19 (!OE2), R109.1, R118.1, R128.1, R138.1, R148.1, R158.1, R168.1, R178.1; also elsewhere on the board
unnamed: C148.1, D29.3 (A,K), IC8.3 (A1), R113.2, R118.2
unnamed: C149.1, D30.3 (A,K), IC8.4 (A2), R123.2, R128.2
unnamed: C150.1, D31.3 (A,K), IC8.5 (A3), R133.2, R138.2
unnamed: C151.1, D28.3 (A,K), IC8.2 (A0), R109.2, R198.2
unnamed: C152.1, D32.3 (A,K), IC8.6 (A4), R143.2, R148.2
unnamed: C153.1, D33.3 (A,K), IC8.7 (A5), R153.2, R158.2
unnamed: C154.1, D34.3 (A,K), IC8.8 (A6), R163.2, R168.2
unnamed: C155.1, D35.3 (A,K), IC8.9 (A7), R173.2, R178.2
PROT_DINPUT_0: IC8.18 (Y0); also elsewhere on the board
PROT_DINPUT_1: IC8.17 (Y1); also elsewhere on the board
PROT_DINPUT_2: IC8.16 (Y2); also elsewhere on the board
PROT_DINPUT_3: IC8.15 (Y3); also elsewhere on the board
PROT_DINPUT_4: IC8.14 (Y4); also elsewhere on the board
PROT_DINPUT_5: IC8.13 (Y5); also elsewhere on the board
PROT_DINPUT_6: IC8.12 (Y6); also elsewhere on the board
PROT_DINPUT_7: IC8.11 (Y7); also elsewhere on the board

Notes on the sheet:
14. Digital Input

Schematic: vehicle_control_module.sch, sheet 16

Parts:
C20, C21: 0.1uF; C0603
C22: 1000pF; C0603
J2: 2305018-2; TE_2305018-2
J3, J4, J5, J6, J7, J8, J9, J12: 1017505
J10: 5-2337992-3; 523379923
J11, J13: 2301843-1; 23018431
R26, R27, R28, R29: 75; R0603
R30, R33: 1k; R0603
R86, R87: 5.11k; R0603

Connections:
DEBUG_ETH_LED0: R30.1; also elsewhere on the board
DEBUG_ETH_LED1: R33.1; also elsewhere on the board
DEBUG_ETH_RXM: J10.P6; also elsewhere on the board
DEBUG_ETH_RXP: J10.P3; also elsewhere on the board
DEBUG_ETH_TXM: J10.P2; also elsewhere on the board
DEBUG_ETH_TXP: J10.P1; also elsewhere on the board
DEBUG_USB_DM: J2.A7 (DA_N), J2.B7 (DB_N); also elsewhere on the board
DEBUG_USB_DP: J2.A6 (DA_P), J2.B6 (DB_P); also elsewhere on the board
GND: C20.2, C21.2, C22.2, J2.A1 (GNDA), J2.A12 (GNDA), J2.B1 (GNDB), J2.B12 (GNDB), J2.G1 (GND), J2.G2 (GND), J2.S1 (SHIELD), J2.S2 (SHIELD), J2.S3 (SHIELD), J2.S4 (SHIELD), J10.MH1, J10.MH2, J10.P12 (CATHODE_GREEN), J10.P14 (CATHODE_YELLOW), J11.5, J11.MH1, J11.MH2, J13.5, J13.MH1, J13.MH2, R86.1, R87.1; also elsewhere on the board
unnamed: J10.P13 (ANODE_YELLOW), R33.2
unnamed: C20.1, J10.P4
unnamed: J10.P5, R26.2
unnamed: C21.1, J10.P7
unnamed: J10.P8, R27.2
unnamed: J10.P11 (ANODE_GREEN), R30.2
unnamed: J10.P10, R28.2
unnamed: J10.P9, R29.2
unnamed: C22.1, R26.1, R27.1, R28.1, R29.1
unnamed: J2.A5 (CC1), R86.2
unnamed: J2.B5 (CC2), R87.2
RS232_PORT0_RX: J11.2; also elsewhere on the board
RS232_PORT0_TX: J11.3; also elsewhere on the board
RS232_PORT1_RX: J13.2; also elsewhere on the board
RS232_PORT1_TX: J13.3; also elsewhere on the board

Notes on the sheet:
Power
Ethernet
CAN
Green LED = Serial Link is Up Yellow LED = Signal Detected
15. Connectors

Board: 2 copper layers, 496 parts (0 on the bottom side), 365 nets, no tracks yet.

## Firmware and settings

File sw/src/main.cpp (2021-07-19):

#include <board.h>
#include <conf_features.h>

#include <chip_id_helper.h>
#include <mac_address.h>

#include <task_adc.h>
#include <task_ethernet.h>
#include <task_led.h>
#include <task_lua.h>

#include <lua.h>

#include <FreeRTOS.h>
#include <task.h>

#include <FreeRTOS_IP.h>

#include <chipid.h>
#include <efc.h>
#include <ethernet_phy.h>
#include <fpu.h>
#include <rstc.h>
#include <serial.h>
#include <stdio_serial.h>
#include <twihs.h>

#include <array>
#include <cstring>


static void configure_console()
{
    constexpr usart_serial_options_t uart_serial_options = {
        .baudrate = CONF_UART_BAUDRATE,
        .charlength = CONF_UART_CHAR_LENGTH,
        .paritytype = CONF_UART_PARITY,
        .stopbits = CONF_UART_STOP_BITS,
    };

    /* Configure console UART. */
    stdio_serial_init(CONF_UART, &uart_serial_options);

    /* Specify that stdout should not be buffered. */
    setbuf(stdout, NULL);
}

static Eui48MacAddress at24mac_get_mac_address()
{
    Eui48MacAddress mac_addr = {};

    /* MAC address */
    twihs_packet_t packet_mac_addr = {};

    packet_mac_addr.chip = BOARD_AT24MAC_EXTENDED_ADDRESS;
    packet_mac_addr.addr[0] = 0x9A;
    packet_mac_addr.addr_length = 1;
    packet_mac_addr.buffer = &(mac_addr[0]);
    packet_mac_addr.length = mac_addr.size();

    if (TWIHS_SUCCESS != twihs_master_read(BOARD_AT24MAC_TWIHS, &packet_mac_addr))
    {
        printf("Failed twihs_master_read init.\n\r");
    }

    if ((mac_addr[0] == 0xFC) || (mac_addr[1] == 0xC2) || (mac_addr[2] == 0x3D))
    {
        mac_addr.unique = true;
    }

    return mac_addr;
}

static const char* get_reset_reason()
{
    uint32_t cause = rstc_get_reset_cause(RSTC);
    //! [reset_get_status]

    /* Decode the reset reason. */
    switch (cause)
    {
        case RSTC_GENERAL_RESET:
            return "General Reset";
            break;

        case RSTC_BACKUP_RESET:
            return "Backup Reset";
            break;

        case RSTC_WATCHDOG_RESET:
            return "Watchdog Reset";
            break;

        case RSTC_SOFTWARE_RESET:
            return "Software Reset";
            break;

        case RSTC_USER_RESET:
            return "User Reset";
            break;

        default:
            return "Invalid reset reason!";
    }
}

int main()
{
    /* Initialize the SAM system */
    sysclk_init();
    board_init();

    /* Initialize the console uart */
    configure_console();

    chipid_data_t chipid_data = {};
    chipid_read(CHIPID, &chipid_data);

    /* Output demo information. */
    printf("Board: " BOARD_NAME "\n\r");
    printf("%s (%s)\n\r", get_chip_id_arch_str(chipid_data.ul_arch),
        get_chip_id_embedded_processor_type_str(chipid_data.ul_eproc));
    printf("%s (NVM: %s, NVM2: %s)\n\r", get_chip_id_nvp_type_str(chipid_data.ul_nvptyp),
        get_chip_id_nvm_size_str(chipid_data.ul_nvpsiz), get_chip_id_nvm2_size_str(chipid_data.ul_nvpsiz2));
    printf("SRAM: %s\n\r", get_chip_id_sram_size_str(chipid_data.ul_sramsiz));
    printf("Sysclock: %ld MHz\n\r", sysclk_get_cpu_hz() / 1000000UL);
    printf("FPU enabled: %s\n\r", fpu_is_enabled() ? "true" : "false");
    printf("Reset cause: %s\n\r", get_reset_reason());

    if constexpr (features::kReadFlashUniqueId)
    {
        // Purposedly keep around another byte to null terminate.
        uint32_t unique_id[5] = {};

        if (EFC_RC_OK != efc_perform_read_sequence(EFC, EFC_FCMD_STUI, EFC_FCMD_SPUI, &(unique_id[0]), 4))
        {
            printf("Failed Read the unique identifier!\n\r");
            return 0;
        }

        printf("Unique ID: %s\n\r", reinterpret_cast<char*>(&(unique_id[0])) + 1U);
    }

    Eui48MacAddress mac_addr = {};
    if constexpr (features::kReadMacFromEeprom)
    {
        mac_addr = at24mac_get_mac_address();
    }

    printf("MAC Address (%s): %02X:%02X:%02X:%02X:%02X:%02X\n\r", mac_addr.unique ? "Unique" : "Hardcoded",
        mac_addr[0], mac_addr[1], mac_addr[2], mac_addr[3], mac_addr[4], mac_addr[5]);
    printf("IP Address: %d.%d.%d.%d\n\r", ETHERNET_CONF_IPADDR0, ETHERNET_CONF_IPADDR1, ETHERNET_CONF_IPADDR2,
        ETHERNET_CONF_IPADDR3);


    printf("-- Compiled (" BUILD_TYPE "): " __DATE__ " " __TIME__ "\n\r");
    printf("-- FreeRTOS " tskKERNEL_VERSION_NUMBER "\n\r");
    printf("-- " LUA_VERSION "\n\r");

    if (false == create_task_led())
    {
        printf("Failed to create LED task.\r\n");
    }

    if (false == create_task_adc())
    {
        printf("Failed to create ADC task.\r\n");
    }

    if constexpr (features::kEnableLua)
    {
        if (false == create_task_lua())
        {
            printf("Failed to create Lua task.\r\n");
        }
    }

    if constexpr (features::kEnableEthernet)
    {
        if (false == create_task_ethernet(mac_addr))
        {
            printf("Failed to create Ethernet task.\n\r\n");
        }
    }

    if constexpr (features::kEnableICache)
    {
        SCB_EnableICache();
    }

    if constexpr (features::kEnableDCache)
    {
        SCB_EnableDCache();
    }

    traceSTART();

    /* Start the scheduler. */
    vTaskStartScheduler();

    /* Will only get here if there was insufficient memory to create the idle task. */
    return 0;
}

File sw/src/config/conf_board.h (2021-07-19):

#ifndef CONF_BOARD_H_
#define CONF_BOARD_H_

#include <cstdbool>

namespace board
{

/* Configure UART pins */
constexpr bool kEnableUartConsole = true;
constexpr bool kDisableWatchdogAtInit = true;
constexpr bool kConfigureMpuAtInit = false;
constexpr bool kEnableCacheAtInit = false;
constexpr bool kEnableTcmAtInit = false;

constexpr bool kEnableTwi = true;

constexpr bool kEnableEthernet = true;

constexpr bool kEnableCan0 = false;
constexpr bool kEnableCan1 = false;

constexpr bool kEnableSpi = false;
constexpr bool kEnableQspi = false;

constexpr bool kEnablePwmLed0 = false;
constexpr bool kEnablePwmLed1 = false;

constexpr bool kConfigureUsartRxd = false;
constexpr bool kConfigureUsartTxd = false;
constexpr bool kConfigureUsartSck = false;
constexpr bool kConfigureUsartCts = false;
constexpr bool kConfigureUsartRts = false;

constexpr bool kEnableSdMmc = false;
constexpr bool kEnableLcd = false;

constexpr bool kEnableUsb = false;
constexpr bool kConfigureUsbVbusDetect = false;
constexpr bool kConfigureUsbIdDetect = false;

constexpr bool kEnableSdram = false;

constexpr bool kEnableIsi = false;

constexpr bool kConfigureHighsides = true;

}  // namespace board

#endif  // CONF_BOARD_H_

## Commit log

2020-01-01 Initial commit, add WIP hardware
    [vehicle_control_module.brd, vehicle_control_module.sch]
2020-01-01 Swap EEPROM with QSPI Flash, still has 48-bit EUI
    [vehicle_control_module.brd, vehicle_control_module.sch]
2020-01-02 Add JTAG connector
    [vehicle_control_module.brd, vehicle_control_module.sch]
2020-01-05 Flesh out FTDI and RS232
    [vehicle_control_module.brd, vehicle_control_module.sch]
2020-01-06 Start adding power supply
    [vehicle_control_module.brd, vehicle_control_module.sch]
2020-01-12 Add LTE modem and flesh out CAN interface
    [vehicle_control_module.brd, vehicle_control_module.sch]
2020-01-12 First stab at power supply
    [vehicle_control_module.brd, vehicle_control_module.sch]
2020-01-13 Switch 3V3 LDO to fix compatibility with EN pins
    [vehicle_control_module.brd, vehicle_control_module.sch]
2020-01-13 Add high side drivers
    [vehicle_control_module.brd, vehicle_control_module.sch]
2020-01-26 Swap to simple CAN transciever, no wake on CAN functionality required
    [vehicle_control_module.brd, vehicle_control_module.sch]
2020-01-27 Add digital inputs, connect MCU power supply
    [vehicle_control_module.brd, vehicle_control_module.sch]
2020-02-02 Fix connection between MCU and switch
    [vehicle_control_module.brd, vehicle_control_module.sch]
2020-02-02 Add Debug LEDs
    [vehicle_control_module.brd, vehicle_control_module.sch]
2020-02-03 Add schematic for test tool based on the full vehicle control module design
    [testtool.sch, vehicle_control_module.brd]
2020-02-22 Add missing oscillator, start to layout testtool board
    [testtool.brd, testtool.sch, vehicle_control_module.brd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]
2020-02-23 Finish placing components for testtool
    [testtool.brd]
2020-03-08 Finish laying out the test tool
    [testtool.brd, testtool.sch]
2020-03-08 Fix silkscreen
    [testtool.brd]
2020-03-13 Add BOM for testtool
    [bom.xlsx]
2020-05-19 First working bringup of board SW on FreeRTOS
2020-11-16 Move example GMAC driver out from FreeRTOS portable and start cleaning it up. Add iperf server for testing.
2021-06-24 Add very crude ADC support from ASF example
2021-07-19 Start to rough in ADC and PWM support for highsides
